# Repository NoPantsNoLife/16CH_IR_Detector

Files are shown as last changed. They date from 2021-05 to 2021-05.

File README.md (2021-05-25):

# 16CH_IR_Detector

## 设计目的

用于巡线小车的16路红外灰度传感器，输出为模拟量灰度，也可选择将ADC芯片拆除后安装比较器芯片和移位寄存器芯片，作为16路单阈值开关量传感器使用。

## 系统概况

### 光电传感器

光电传感器使用亿光的ITR8307/S17/TR8(B)，表贴一体红外对管，自带红外滤光，实测不会受到可见光的影响

### ADC

采用德州仪器(Texas Instruments, TI)的ADS7953 ADC芯片。该芯片为12位ADC，最大采样率为1MSps，有16路MUX输入，数字接口为SPI，本次采用的为TSSOP38封装。

### 基准

PCB上预留了REF5030(3.0V，实际采用)/REF5025(2.5V)/LT1009(2.5V)的芯片位置，并预留微调电位器位置，方便根据采购情况使用不同的基准芯片和对电压进行微调

### 比较器/移位寄存器

预留4个LM339比较器(共16路)和74HC165移位寄存器(2片级联，共16路输入)芯片位置，如有需要可将ADC部分元件空贴，将比较器和移位寄存器部分的元件装上，既可作为使用串行通信的16路单阈值的开关量传感器使用，可减轻MCU的运算负担。本次比赛中未使用此功能

### 电源

GND未进行划分，VCC划分为AVCC和DVCC，采用简单的PI滤波器进行隔离

## 使用方法

### 基本原理

#### 模拟量输出模式

通过SPI接口(软硬件均可)向ADS7953发送读取通道指令，读取1-16号输入的电压，即为1-16个传感器的灰度模拟量

#### 单阈值开关量输出模式

(未做验证)由于74HC165的时序也符合SPI，可直接利用SPI接口读取16位的方式进行通信，每一位对应一个传感器的输出

## 驱动使用说明

此处仅提供模拟量传感器的驱动，基于STM32平台，使用LL库操作SPI和GPIO

### Structure

#### 	ADS7953_Typedef

		定义于ADS7953.h中

##### 	数据域

###### 		SPI_TypeDef* SPI_Port;

			硬件SPI的SPI端口号

###### 		GPIO_TypeDef* NSS_GPIO_Port;

			NSS引脚的所在的GPIO端口组

###### 		uint32_t NSS_GPIO_Pin;

			NSS所在GPIO的Pin号

###### 		enum {ADS7953_Range_VREF=0, ADS7953_Range_2VREF=1} ADC_Range;

			ADC的输入范围参数，决定满量程为VREF或者2倍VREF

### API

#### void ADS7953_ReadChannels(ADS7953_Typedef* ADCx, uint16_t bfr[16], uint16_t channel)

##### 功能

	读取ADS7953的通道输入电压

##### 参数

###### 	ADS7953_Typedef* ADCx

		ADS7953的定义结构体，包含ADS7953的配置参数

###### 	uint16_t bfr[16]

		用于存储通道数据的数组，对应编号通道的数据存放在该数组对应下标处，如CH11的数据将在bfr[11]中存储

###### 	uint16_t channel

		通道掩码输入

		可选：

			ADS7953_Channel_0

			ADS7953_Channel_1

			ADS7953_Channel_2

			ADS7953_Channel_3

			ADS7953_Channel_4

			ADS7953_Channel_5

			ADS7953_Channel_6

			ADS7953_Channel_7

			ADS7953_Channel_8

			ADS7953_Channel_9

			ADS7953_Channel_10

			ADS7953_Channel_11

			ADS7953_Channel_12

			ADS7953_Channel_13

			ADS7953_Channel_14

			ADS7953_Channel_15

			ADS7953_Channel_All

##### 返回值

	无

##### 说明

	掩码可以使用或运算符的形式输入，如 ADS7953_Channel_8 | ADS7953_Channel_14，将会读取8和14号通道

	输出结果在数组中与下标一一对应，例如即使只读取一个ADS7953_Channel_14，也会将数据存储在bfr[14]中，而不是bfr[0]

##### 使用范例

```c
//SPI should be initialized before using
uint16_t ADS7953_F_bfr[16];

ADS7953_Typedef ADS7953_F;
ADS7953_F.ADC_Range = ADS7953_Range_VREF;
ADS7953_F.SPI_Port = SPI6;
ADS7953_F.NSS_GPIO_Pin = SPI6_NE1_Pin;
ADS7953_F.NSS_GPIO_Port = SPI6_NE1_GPIO_Port;

//get all 16 channels' data
ADS7953_ReadChannels(&ADS7953_F, ADS7953_F_bfr, ADS7953_Channel_All);
```

### Typedef

#### ADS7953_Channel_0

ADC通道0的掩码

#### ADS7953_Channel_1

ADC通道1的掩码

#### ADS7953_Channel_2

ADC通道2的掩码

#### ADS7953_Channel_3

ADC通道3的掩码

#### ADS7953_Channel_4

ADC通道4的掩码

#### ADS7953_Channel_5

ADC通道5的掩码

#### ADS7953_Channel_6

ADC通道6的掩码

#### ADS7953_Channel_7

ADC通道7的掩码

#### ADS7953_Channel_8

ADC通道8的掩码

#### ADS7953_Channel_9

ADC通道9的掩码

#### ADS7953_Channel_10

ADC通道10的掩码

#### ADS7953_Channel_11

ADC通道11的掩码

#### ADS7953_Channel_12

ADC通道12的掩码

#### ADS7953_Channel_13

ADC通道13的掩码

#### ADS7953_Channel_14

ADC通道14的掩码

#### ADS7953_Channel_15

ADC通道15的掩码

#### ADS7953_Channel_All

ADC全部通道的掩码

## 驱动移植说明

### 需要修改的函数

#### __INLINE void ADS7953_SPI_Enable(ADS7953_Typedef* ADCx)

##### 	功能

		ADS7953使能(NSS线拉低)

##### 	参数

###### 		ADS7953_Typedef* ADCx

			ADS7953配置结构体，存储了ADS7953的配置

##### 	返回值

		无

#### __INLINE void ADS7953_SPI_Disable(ADS7953_Typedef* ADCx)

##### 	功能

		ADS7953失能(NSS线拉高)

##### 	参数

###### 		ADS7953_Typedef* ADCx

			ADS7953配置结构体，存储了ADS7953的配置

##### 	返回值

		无

#### uint16_t ADS7953_SPI_ReadWriteFrame(ADS7953_Typedef* ADCx, uint16_t TxDat)

##### 	功能

		ADS7953的SPI读写函数，向ADS7953发送或接收一帧(16bit)数据

##### 	参数

###### 		ADS7953_Typedef* ADCx

			ADS7953配置结构体，存储了ADS7953的配置

###### 		uint16_t TxDat

			发送给ADS7953的16bit数据

##### 	返回值

		从ADS7953接收到的16bit数据

### 外部调用的函数

#### void delay(uint32_t t)

##### 	功能

		简单的延时函数，用于提供ADS7953读取每一帧之间的延时

		此处延时没有使用精确的时间单位，与芯片实际运行速度有关，可以修改ADS7953_INTER_FRAME_DELAY的值

		在SPI速度不高时可以取消，请根据具体应用环境决定

##### 	参数

###### 		uint32_t t

			延时时长

##### 	返回值

		无

## 其他说明

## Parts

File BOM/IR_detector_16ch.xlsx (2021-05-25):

Comment | Description | Designator | Footprint | LibRef | Quantity
0 | Resistor | R6 | 0402 | Res | 1
22 |  | RP13 | 8P4R-0603 | 8P4R_F | 1
180 |  | RP1, RP2, RP3, RP4 | 8P4R-0603 | 8P4R_F | 4
0.1uF |  | C2, C4, C5, C7, C12, C19, C48 | 0402 | Cap | 7
10uF |  | C8, C47 | 0402 | Cap | 2
10uH | Inductor | L1 | 0603 | Inductor | 1
1uF |  | C1, C3, C6, C9, C18, C49 | 0402 | Cap | 6
6.8K |  | RP5, RP6, RP7, RP8 | 8P4R-0603 | 8P4R_F | 4
ADS7953SBDBT | 12 bit, 1 MSPS, 16 ch, single ended, micro power, sr i/f, SAR ADC | U23 | TSSOP-38_L9.7-W4.4-P0.50-LS6.4-BL | ADS7953SBDBT | 1
ITR8307/S17/TR8(B) |  | U5, U6, U7, U8, U9, U10, U11, U12, U13, U14, U15, U16, U17, U18, U19, U20 | OPTO-SMD_ITR8307-S17-TR8-B-TS | ITR8307/S17/TR8(B) | 16
REF5030 |  | U22 | VSSOP-8_L3.0-W3.0-P0.65-LS5.0-BL | REF50xx | 1
XH_10P |  | J1 | XH_10P直插弯针 | XH_10P | 1
(NC)0.1uF |  | C10, C14, C15, C16, C17, C20, C21, C22, C23 | 0402 | Cap | 9
(NC)10K |  | R4 | 3x3_ResPot | ResPot | 1
(NC)10K |  | R7 | 3362W-TH_3P-L7.1-W6.9-P2.54-BL-BS | ResPot | 1
(NC)1K |  | RP9, RP10, RP11, RP12 | 8P4R-0603 | 8P4R_F | 4
(NC)1uF |  | C11, C13 | 0402 | Cap | 2
(NC)LM339 |  | U1, U2, U3, U4 | SOP-14_L8.6-W3.9-P1.27-LS6.0-BL | LM339 | 4
(NC)LT1009 |  | U21 | SOP-8_L5.0-W4.0-P1.27-LS6.0-BL | LT1009-SOP8 | 1
(NC)74HC165 | 8-bit parallel-in/serial-out shift register | U24, U25 | SOP-16_L10.0-W3.9-P1.27-LS6.0-BL | 74_165 | 2
(NC)0 | Resistor | R12 | 0402 | Res | 1
(NC)150 | Resistor | R2 | 0402 | Res | 1
(NC)1k | Resistor | R5 | 0402 | Res | 1
(NC)470 | Resistor | R3 | 0402 | Res | 1

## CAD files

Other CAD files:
Mechanical/循迹模块尺寸.DWG

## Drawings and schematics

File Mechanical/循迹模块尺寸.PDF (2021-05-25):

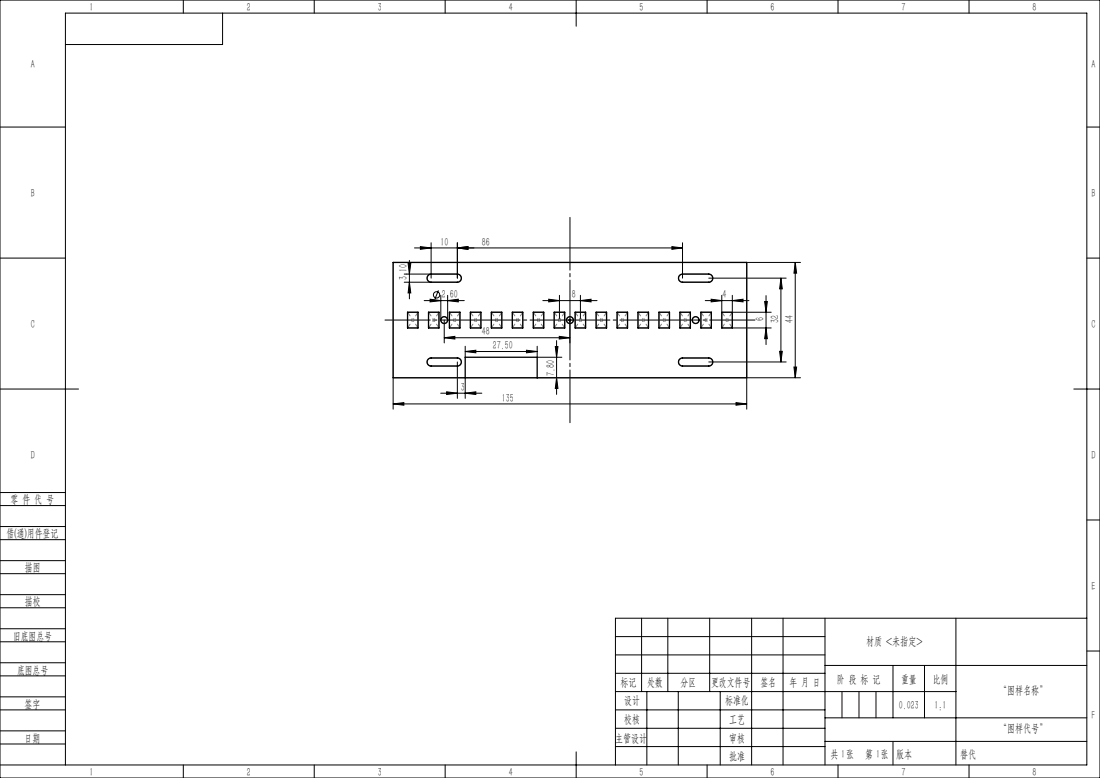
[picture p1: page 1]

材质 <未指定>

阶 段 标 记 | 重量 | 比例 | “图样名称”

标记 | 处数 | 分区 | 更改文件号 | 签名 | 年 月 日
设计 | | | 标准化 | | | | | 0.023 | 1:1
校核 | | | 工艺
主管设计 | | | 审核

“图样代号”

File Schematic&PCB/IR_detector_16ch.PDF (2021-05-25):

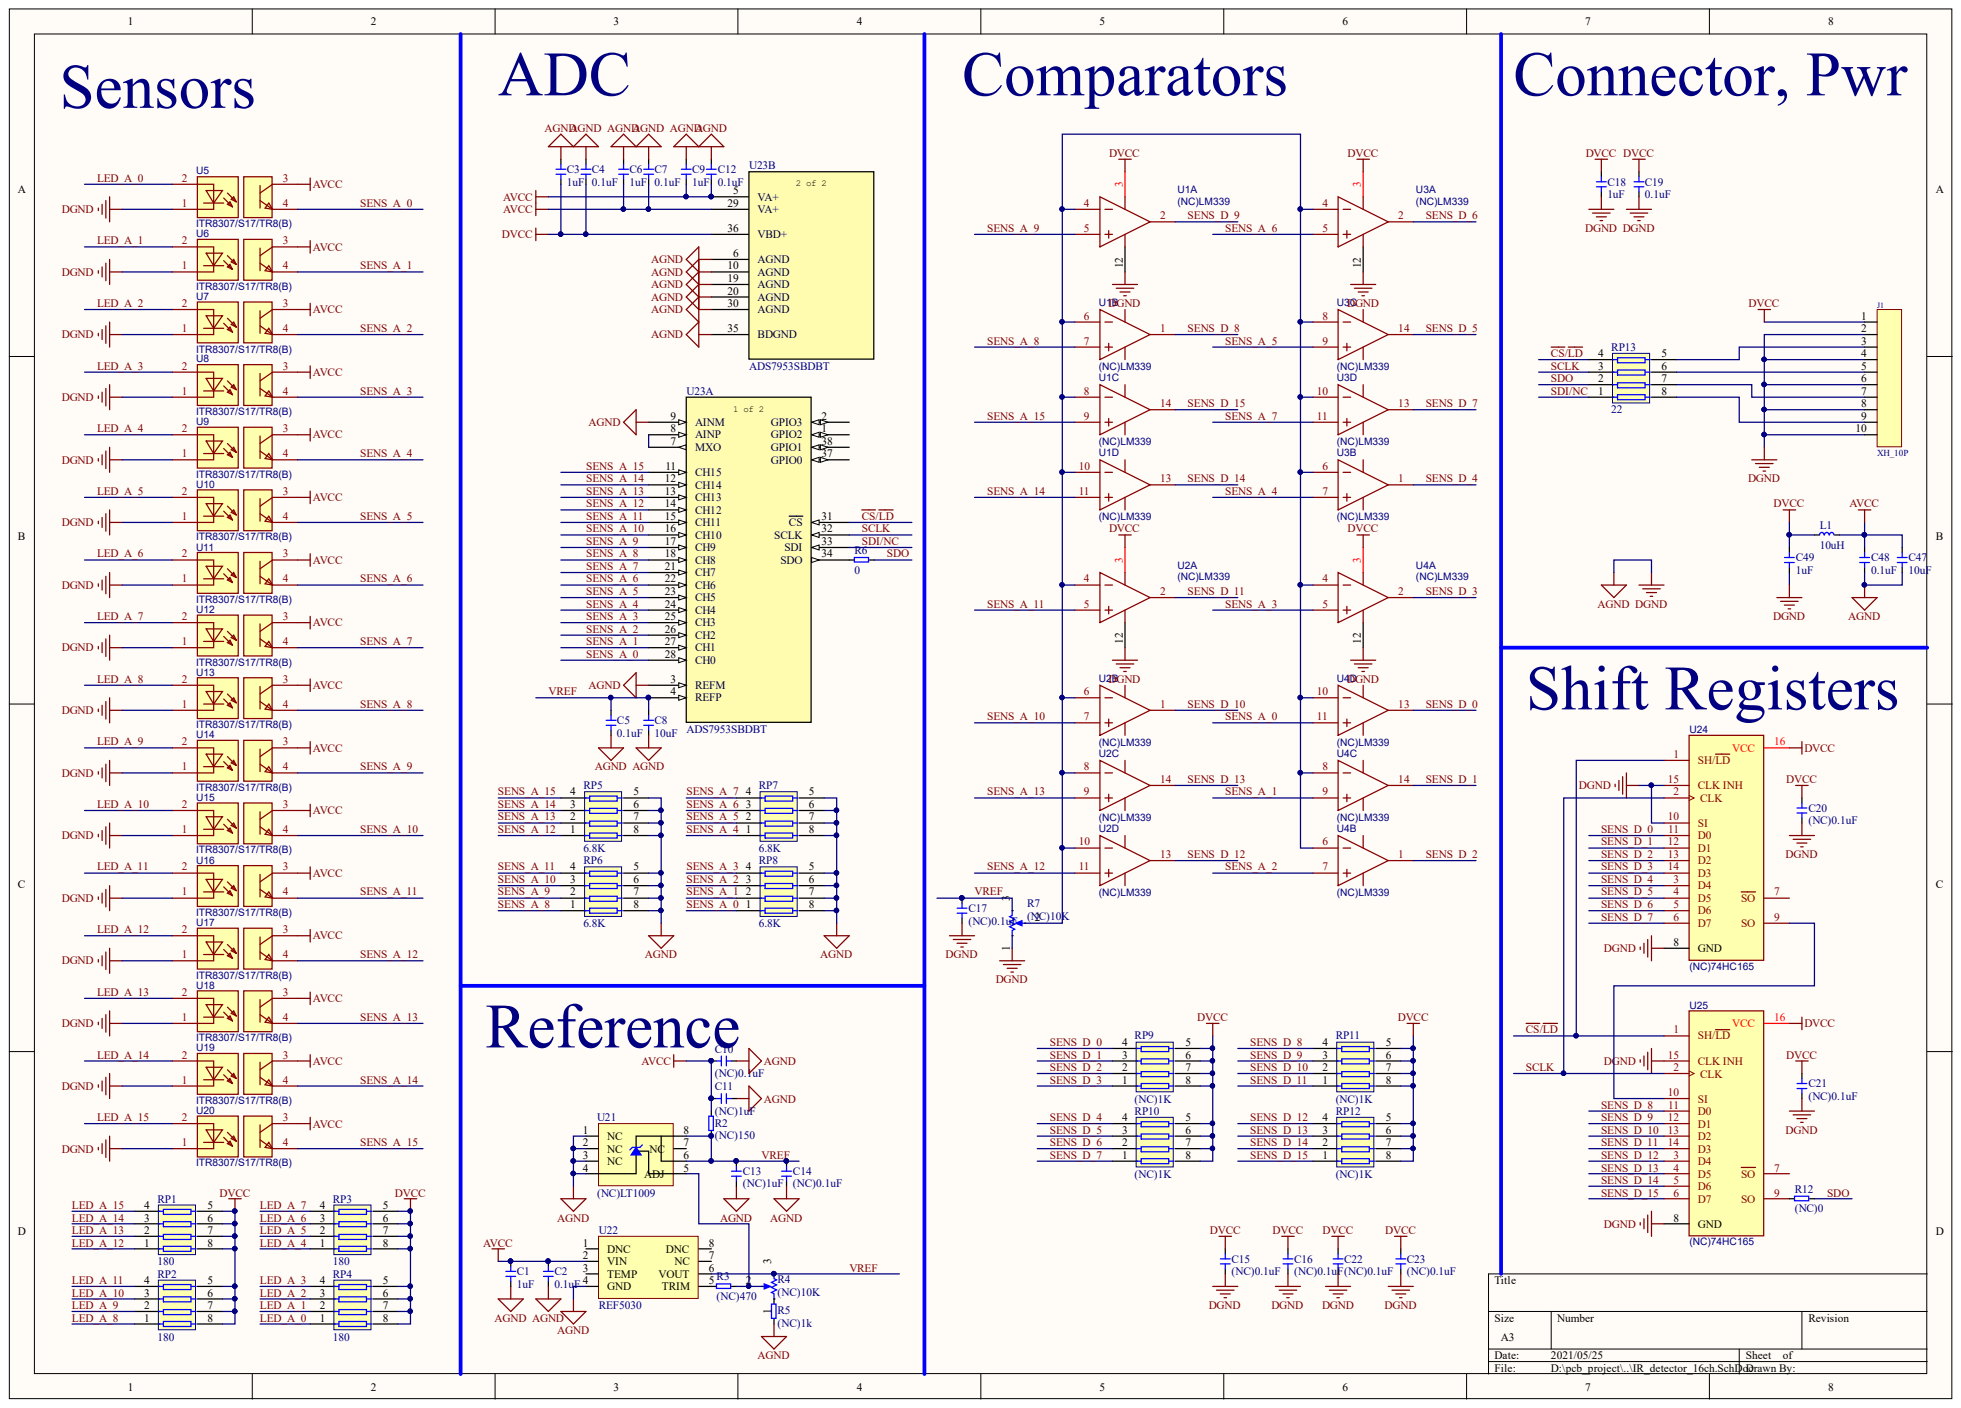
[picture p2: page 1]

6 | L E D_A_6 3 | 6
7 | L E D_A_5 2 | 7

6 | L E D_A_2 3 | 6
7 | L E D_A_1 2 | 7
8 | L E D_A_0 1 | 8

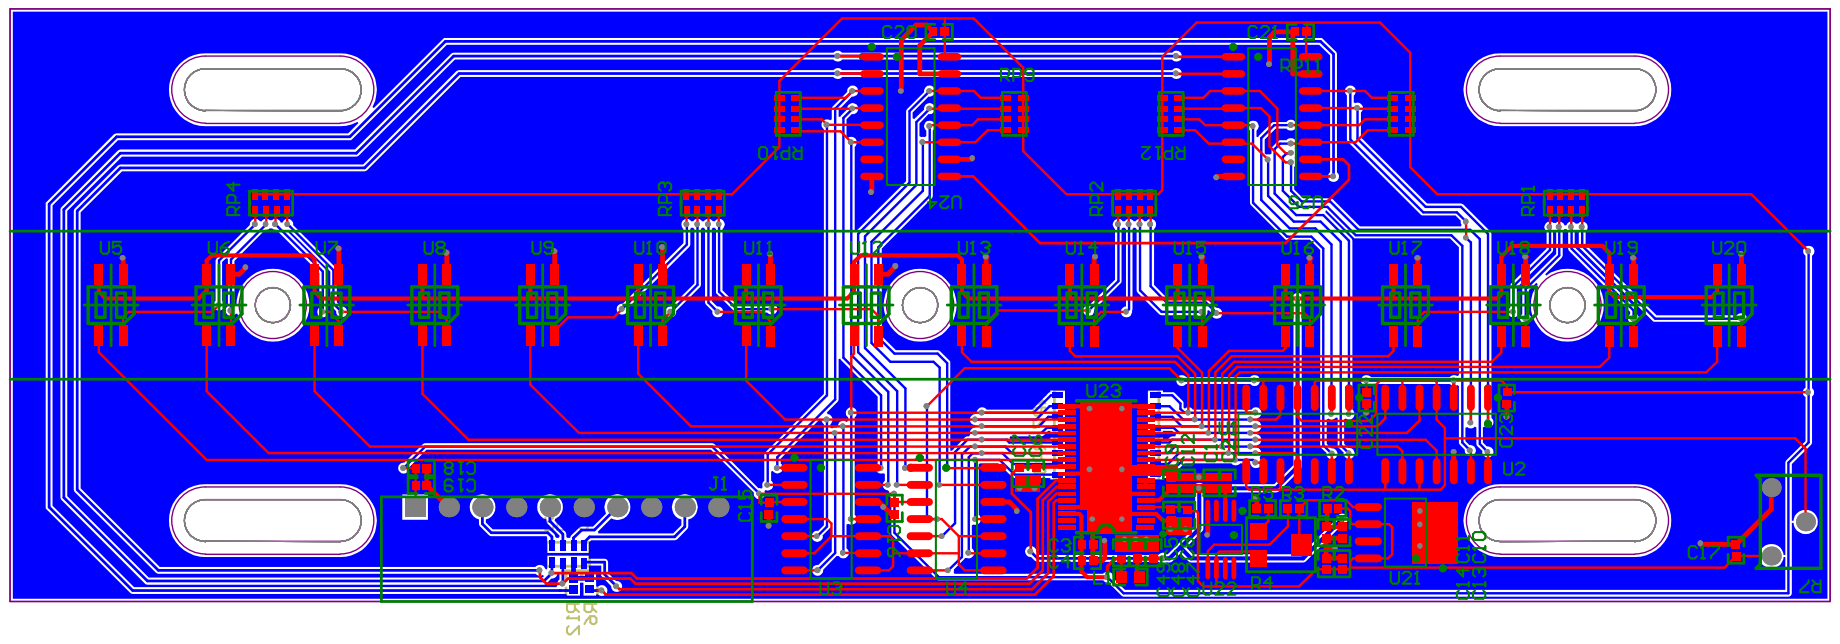
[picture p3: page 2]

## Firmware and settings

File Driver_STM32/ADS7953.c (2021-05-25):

#include "ADS7953.h"

#include "spi.h"
#include "delay.h"


__INLINE void ADS7953_SPI_Enable(ADS7953_Typedef* ADCx);
__INLINE void ADS7953_SPI_Disable(ADS7953_Typedef* ADCx);
uint16_t ADS7953_SPI_ReadWriteFrame(ADS7953_Typedef* ADCx, uint16_t TxDat);


void ADS7953_ReadChannels(ADS7953_Typedef* ADCx, uint16_t bfr[16], uint16_t channel)
{
	uint8_t chNum = 0, i;
	uint16_t RxFrame, ch=channel;
	while(ch)
	{
		if (ch & 0x1)
			chNum++;
		ch >>= 1;
	}
	
	ADS7953_SPI_Enable(ADCx);
	ADS7953_SPI_ReadWriteFrame(ADCx, 0x8000); //Enter Auto-1 Programming Mode
	ADS7953_SPI_Disable(ADCx);
	delay(ADS7953_INTER_FRAME_DELAY);
	
	ADS7953_SPI_Enable(ADCx);
	ADS7953_SPI_ReadWriteFrame(ADCx, channel); //Send Channel Mask
	ADS7953_SPI_Disable(ADCx);
	delay(ADS7953_INTER_FRAME_DELAY);
	
	for(i=0; i<chNum; i++)
	{
		ADS7953_SPI_Enable(ADCx);
		RxFrame = ADS7953_SPI_ReadWriteFrame(ADCx, ADCx->ADC_Range == ADS7953_Range_2VREF ? 0x2840 : 0x2800);
		ADS7953_SPI_Disable(ADCx);
		bfr[RxFrame >> 12] = RxFrame & 0xfff;
		delay(ADS7953_INTER_FRAME_DELAY);
	}
}


uint16_t ADS7953_SPI_ReadWriteFrame(ADS7953_Typedef* ADCx, uint16_t TxDat)
{
	uint16_t Rx;
	Rx  = SPI_ReadWriteByte(ADCx->SPI_Port, TxDat >> 8) << 8;
	Rx |= SPI_ReadWriteByte(ADCx->SPI_Port, TxDat & 0xff);
	return Rx;
}


__INLINE void ADS7953_SPI_Enable(ADS7953_Typedef* ADCx)
{
	LL_GPIO_ResetOutputPin(ADCx->NSS_GPIO_Port, ADCx->NSS_GPIO_Pin);
}


__INLINE void ADS7953_SPI_Disable(ADS7953_Typedef* ADCx)
{
	LL_GPIO_SetOutputPin(ADCx->NSS_GPIO_Port, ADCx->NSS_GPIO_Pin);
}

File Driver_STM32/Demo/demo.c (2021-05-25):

#include "ADS7953.h"

void main()
{
	uint16_t ADS7953_F_bfr[16];  //buffer for ADC Data
	
	ADS7953_Typedef ADS7953_F;  //struct for ADS7953 Configuration
	ADS7953_F.ADC_Range = ADS7953_Range_VREF;
	ADS7953_F.SPI_Port = SPI6;
	ADS7953_F.NSS_GPIO_Pin = SPI6_NE1_Pin;
	ADS7953_F.NSS_GPIO_Port = SPI6_NE1_GPIO_Port;
	
	
	SPI_Init();
	//SPI should be initialized before using
	
	//you don't need to initialize ADS7953
	
	while(1)
	{

		ADS7953_ReadChannels(&ADS7953_F, ADS7953_F_bfr, ADS7953_Channel_All);
		//get all 16 channels' data
		
		//do something here
	}
}
